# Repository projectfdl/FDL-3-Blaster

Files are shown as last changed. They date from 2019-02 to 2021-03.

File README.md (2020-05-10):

(https://www.projectfdl.com)

# FDL-3-Blaster

Welcome to the FDL-3 blaster repository

## This project is licensed under the terms of the Creative Commons Non-Commercial Attribution Share Alike 4.0 license
Print it, tweak it, share it and if you do and give us props. Please don't sell it without Project FDL permission.

<br>
<br>

# Operating your FDL-3

## Settings (Applicable to full auto tail, firmware version 1.05)

**Speed**<br>
Value: 0 - 100 : Default: 50<br>
Speed or power setting used to adjust the velocity the blaster fires darts.<br><br>

**ROF (Rate of Fire)**<br>
Value: 0 - 100 : Default: 100<br>
Rate of fire setting to adjust time between each dart fired when in burst or full auto.<br><br>

**Burst**<br>
Value: 1, 2, 3, F : Default: 1<br>
Number of darts fired per single trigger pull. F (full auto) will continue firing darts until you release the trigger.<br><br>

**MinSpin (Minimum Spinup)**<br>
Value: 120 - 500 : Default: 220<br>
Time in milliseconds for motors to spinup between trigger pull and firing dart when speed set to 0.<br><br>

**MaxSpin (Maximum Spinup)**<br>
Value: 150 - 500 : Default: 200<br>
Time in milliseconds for motors to spinup between trigger pull and firing dart when speed set to 100.
Note: MinSpin and MaxSpin together create a range of spinup time. When speed is set to 50, spinup time is half way between MinSpin and MaxSpin. Eg. MinSpin = 200, MaxSpin = 300, Speed = 50. Actual spinup time = 250. Speed = 75. Actual spinup time = 275.<br><br>

**Fire Mode**<br>
Value: SAFE, ABIDE, AUTO, CACHE : Default: ABIDE<br>
Setting for how the blaster reacts to a trigger pull prior to firing a dart.<br>
- Safe: safety mode. Blaster will beep and not fire dart.
- Abide: Trigger abide. Blaster will only fire a dart if trigger is held down for the full spinup duration. If trigger is released prior to the completion of spinupt time, the blaster will not fire.
- Auto: Blaster will fire dart automatically. If trigger is released prior to the completion of spinup time, the blaster will continue it's fire cycle and proceed to fire all darts set by the burst setting.
- Cache: Cached mode. The blaster will "cache" the number of trigger pulls during the spinup duration. If you are able to pull the trigger three times during spinup, the blaster will fire three darts. Twice, two darts. Once, one dart.<br><br>

**Spindown**<br>
Value: 7 - 18 : Default: 14<br>
Rate at which the blasters motors wind down or "spindown" to a stop. Lower is faster. Higher is slower. The value is technically equal to the time in milliseconds to lower the speed of the blaster by a single increment.<br><br>

**Idle (Idle Time)**<br>
Value: 0 - 10 : Default: 0<br>
After the end of a fire cycle the motors will spin at a slow idle speed for this number of seconds. This allows the motors to spinup faster than if they were to start from a dead stop. Setting this to 0 will disable the feature. Note: if the trigger is held down at the end of a fire cycle, the motors will run at this idle speed until trigger is released.<br><br>

**Load**<br>
Load user preset 1, 2, 3 or back out of menu.<br><br>

**Save**<br>
Save current blaster settings to one of three user preset slots which can be recalled later by the load menu or user buttons on the side of the blaster. Note: only settings prior before the Load menu item are stored in presets. Speed, ROF, Burst, MinSpin, MaxSpin, FireMode, Spindown and Idle.<br><br>

**MinSpd (Minimum Speed)**<br>
Value: 0 - 100 : Default: 0<br>
Determines the minimum speed value that may be set by the speed setting. Eg. if set to 25, the speed gauge will not go lower than 25.<br><br>

**MaxSpd (Maximum Speed)**<br>
Value: 0 - 100 : Default: 100<br>
Determines the maximum speed value that may be set by the speed setting. Eg. if set to 80, the speed gauge will not go higher than 80. Recalled presets with higher speed values will default to this setting. The last value this setting was set to prior to powering off the blaster can be locked by flipping the red speed lock switch located on next to the screen on the board in the rear of the blaster. The rear cap piece must be removed to access this switch. This value cannot be altered while the blaster speed lock is enabled.<br><br>

**BtnMode (Button Mode)**<br>
Value: PRESET, SPEED, ROF, BURST : Default: BURST<br>
Determines what the three user quick buttons on the side of the blaster do. These buttons must be briefly held down for action to take place.<br>
- Preset: Loads user preset. Front button loads preset 1. Rear button closed to user loads preset 3.
- Speed: Sets blaster speed. From front to rear button. 50, 75, 100
- ROF: Set blaster rate of fire. From front to rear button. 50, 75, 100
- Burst: Sets blaster burst count. From front to rear button. 1, 2, F<br><br>

**BrkAgr (Braking Aggression)**<br>
Value: 3 - 20 : Default: 16<br>
Determines how aggressively the pusher brakes prior to reaching a stop at the rear of its cycle. Setting lower may produce a more responsive cycle but may leave the pusher extended at the end of the cycle. Setting higher may resolve issues with a pusher that does not stop properly at the rear of its cycle. This setting should rarely need to change.<br><br>

**ULock (User Lock)**<br>
Enable complete blaster lockout by setting a user defined sequence of quick button presses. Blaster will not function once lock is set and may be unlocked by reentering the defined sequence. Note: do not forget your code. While it is possible to reset your blaster, the method of doing so is not described in this document.<br><br>

**Bright (Brightness)**<br>
Value: 0 - 100 : Default: 100<br>
Sets the brightness of the oled display. This is a very subtle change in a high light environment but more obvious in darker surroundings.<br><br>

**Sound**<br>
Value: OFF, ON : Default: ON<br>
Enables or disables audible beeping while navigating menus, loading presets etc.<br><br>

**BatOff (Battery Offset)**<br>
Value: -5 - 5 : Default: 0<br>
Offsets the read battery voltage in increments of 0.1 volts. This is only for use with legacy or self built blasters if a full 3s battery does not read 12.6 volts.<br><br>

**Info**<br>
Displays current firmware version.<br><br>

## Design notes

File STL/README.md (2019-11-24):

(https://www.projectfdl.com)

# Printing your FDL-3

Note: Use your best judgement when slicing nad printing parts. Consider how your printer operates best and what settings you normally use for strong but light parts. This readme should be used as a set of suggestions to get you started but every printer is different. 

- We use common 0.4mm nozzles at 0.2mm layer heights. If using a different size, adjust accordingly.
- We use mostly PLA filament. It prints easily and cleanly without much hassle but can warp in high temperature environments like a hot car. Any other material such as PETG or ABS can be used at your own discretion.
- We typically use 3-5 perimeters (1.2 - 1.6mm) on all parts. Most have 3 but extra are added for structural parts like barrel outers(5), handle cores(4), stock attachment(4) etc
- Infill should be roughly 20% using your favorite infill pattern. Honeycomb and gyroid are great options. Add extra for structural parts like barrel outers(40-50), stock attachment(30) etc
- Prints must be clean and accurate. Too high an extrusion rate can lead to tight fitting parts. Remove and clean any brims or support. Sanding should not be required but may help fitment in areas.
- No support should be necessary on any parts but can help parts with areas of long bridging. Ex. mag gripper and fat boi grip on the 40 nose
- Parts should all be oriented to print. Use your best judgement and don't be afraid to try other orientations.
- Brims are suggested on parts without a lot of bed contact. There are small strands of material across the edges of channels on some parts. These prevent brim from entering wire channels. This should be removed.
- The pusher housing cap has holes that need drilling. Use a 9/64" or xacto blade to clean.
- The pusher housing has holes in it that need drilling. Use a 3mm and 7mm bit or xacto to clean.
- The spinner has a hole in the side that should be tapped with a 10-32 tap. Be careful to keep tool clean and not overheat the part.

Good luck and make on!

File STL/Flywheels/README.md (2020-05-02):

(https://www.projectfdl.com)

# Flywheel Choice

Choose which flywheel to print based off your motor. We ship bundles and blasters with Lumenier LX2205 motors. These are identical in size to the RX2205 which the wheels were based on but purple instead of silver so for FDL-3's #0098+ choose the Lumenier file. FDL-3's prior to #0097 used black Vspec motors with four screws to mount the flywheels. Choose the vspec file for those. The EMAX file is for a motor that was going to be used but never was. It is there for historical purposes. Spacers are only required for the EMAX version and can be ignored. Flywheels for the HIR nose are different but labeled as such.

# Printing

(https://www.projectfdl.com)

Flywheels must be printed balanced and strong but also light weight. Here are a few suggestions for how to do so. 

- We use common 0.4mm nozzles at 0.2mm layer heights. If using a different size, adjust accordingly.
- 0.2mm layer or lower layer height
- We currently print all wheels in ABS. It is extremely heat resistant, impact tolerant and less dense than PLA or PETG thus lighter. It requires an enclosure around your printer and some care to get right but we found it to be our favorite flywheel material. It's also easy to machine for balancing purposes.
- PLA can be used for flywheels with some caveats. Given the short time and ease of use, those caveats may be more or less important in your situation. It can be susceptible to warping under heavy or summer time use but is stronger than PETG in this use. It also fails in a safe way by splitting at layer seams. Good luck getting that to happen though.
- PETG can be weak and shatter if not printed properly. It's higher heat resistance can help warping but use it at your own risk to avoid shattered flywheels, ouch.
- Use 3-4 perimeters. 3 can lead to lighter wheels but 4 will be reliably stronger. We use 4.
- Infill should be roughly 20%, rectilinear, rotated vertical/horizontal instead of the typical 45 degrees and centered on the wheel.
- Layer seams (called different things in different slicers) should be randomized to avoid a heavy side where all the seams line up. Slicers will typically hide these seams in corners. We want them scattered randomly. A "zitted" appearance is normal and can help grip on darts.
- Target roughly 10 gram weight per wheel. Heavier have more inertia and could potentially perform better but are more susceptible to imbalance and sluggish feel. Lighter are less susceptible to imbalance and quieter but provide less momentum.
- Not all flywheels printed in this manner will be perfect. A propeller balancer can be used to balance wheels or you can print multiples and choose the best two.

Good luck and make on!

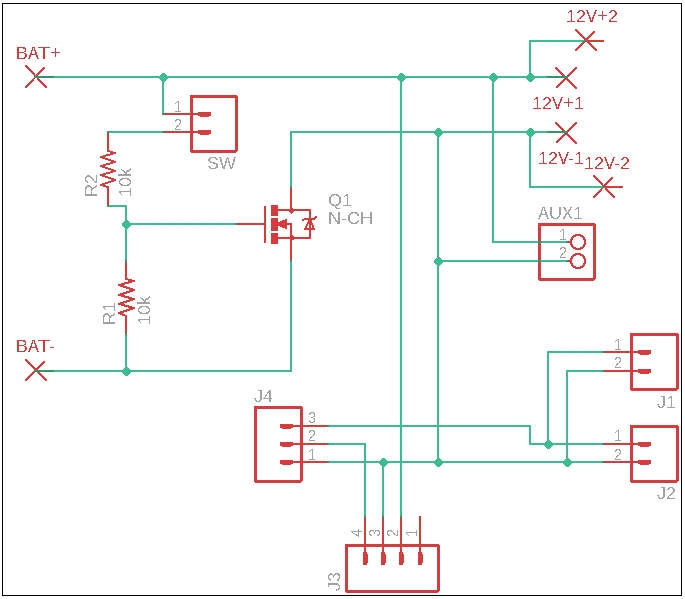
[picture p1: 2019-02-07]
PCB/PWR/FDL-3 PWR PCB Schematic.PNG

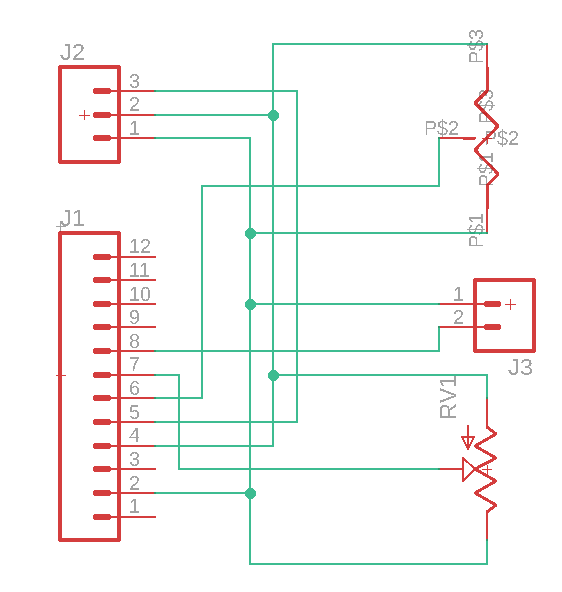
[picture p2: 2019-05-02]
PCB/TRG/FDL-3 TRG PCB Schematic.PNG

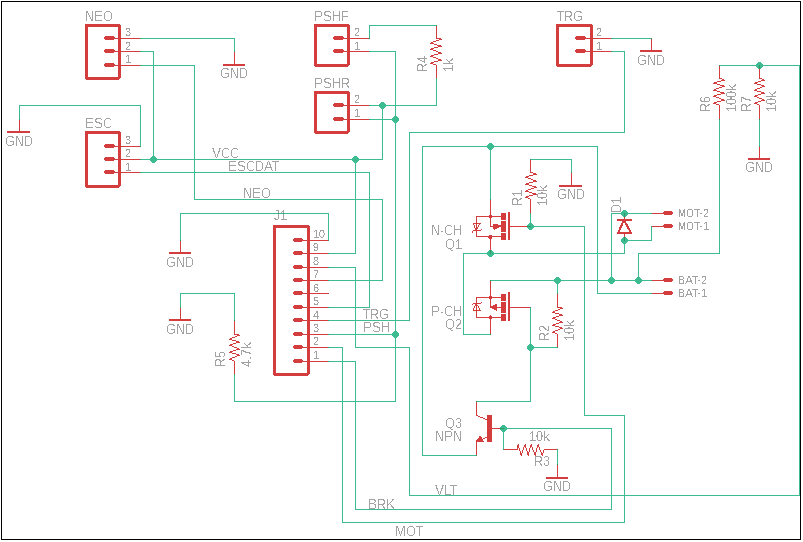
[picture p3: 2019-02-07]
PCB/DCP/FDL-3 DCP PCB Schematic.PNG

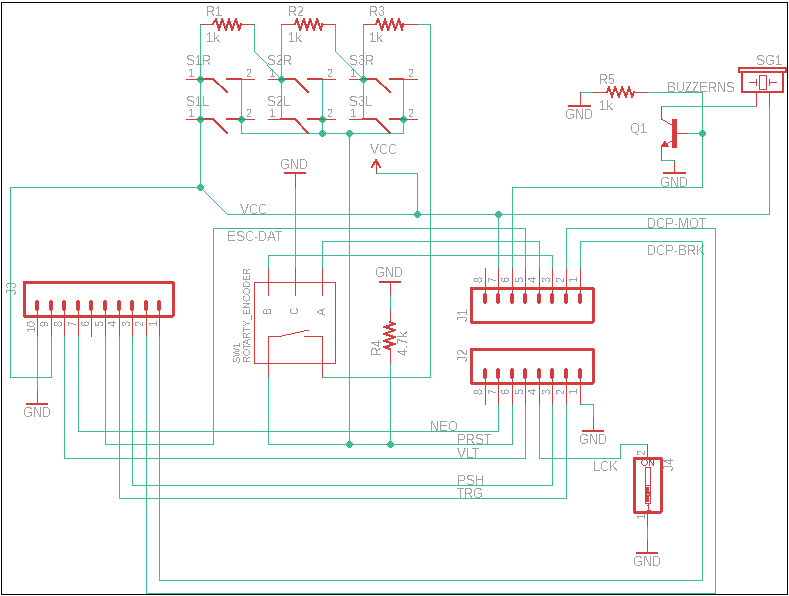
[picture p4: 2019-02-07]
PCB/CTL/FDL-3 CTL PCB Schematic.PNG

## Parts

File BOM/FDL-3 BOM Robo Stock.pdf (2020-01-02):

### FDL-3 ROBO STOCK BOM

Item | Quantity | Link

Hardware
6-32 x 3/8" Machine Screw | 4 | https://www.mcmaster.com/91249A146
6-32 x 1/2" Machine Screw | 4 | https://www.mcmaster.com/91249A148
8-32 x 1/2" Machine Screw | 4 | https://www.mcmaster.com/91249a194
8-32 Coupling Nut | 2 | https://www.mcmaster.com/90264a420
M5 Square Nut | 2 | https://www.mcmaster.com/90225a101
M5x70 Button Head Hex Screw | 2 | https://www.mcmaster.com/92095a484

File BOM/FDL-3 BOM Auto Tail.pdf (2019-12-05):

### FDL-3 AUTO TAIL BOM

Item | Quantity | Link

Hardware
6-32 x 3/8" Machine Screw | 18 | https://www.mcmaster.com/91249A146
6-32 x 1/2" Machine Screw | 9 | https://www.mcmaster.com/91249A148
6-32 x 1" Machine Screw | 1 | https://www.mcmaster.com/91249A159
6-32 Nut | 2 | https://www.mcmaster.com/91841A007
4-40 1-1/4" Hex Screw | 7 | https://www.mcmaster.com/92196A034
4-40 Nylon Lock Nut | 7 | https://www.mcmaster.com/91831A005
10-32 x 3/8" Set Screw Knurled End | 1 | https://www.mcmaster.com/93445A385
M3x6 Hex Screw | 8 | https://www.mcmaster.com/91290A111
Spring (Papermate InkJoy) | 1 | https://www.amazon.com/gp/product/B01EB6E3EC
M3x6 Csnk Hex Screw | 2 | https://www.mcmaster.com/92125A126
6-32 x 3/8" Thumb Screw | 2 | https://www.mcmaster.com/91185A261

DC Pusher Motor
25D Geared Motor ~1000RPM | 1 | https://www.pololu.com/product/3202
22ga Silicon Wire Red/Black Pair | 35cm | https://www.amazon.com/gp/product/B07DZZ83H6
JST Female Housing | 1 | https://www.pololu.com/product/1934
JST Female Crimp Connector | 2 | https://www.pololu.com/product/1934
3/32" Heat Shrink Red | 1.5" | (link unavailable - purchased locally)
3/32" Heat Shrink Black | 1.5" | (link unavailable - purchased locally)
1/8" Heat Shrink Black | 1" x 2 | (link unavailable - purchased locally)

DCP PCB
DCP PCB | 1 | https://projectfdl.myshopify.com/products/fdl-3-pcbs
N Channel Mosfet | 1 | https://www.digikey.com/products/en?keywords=IRLU3410PBF-ND
P Channel Mosfet | 1 | https://www.digikey.com/products/en?keywords=IRFU5505PBF-ND
Flyback Diode | 1 | https://www.digikey.com/product-detail/en/on-semiconductor/UF4007/UF4007CT-ND/965732
NPN Transistor | 1 | https://www.digikey.com/products/en?keywords=2N4401-ND
Header Male 2 Pin | 5 | https://www.pololu.com/product/965
Header Male 3 Pin | 1 | https://www.pololu.com/product/965
Header Female 10 Pin | 1 | https://www.digikey.com/product-detail/en/sullins-connector-solutions/PPTC101LFBN-RC/S7008-ND/810149
Resistor 1k 1/4W 6mm | 1 | https://www.digikey.com/product-detail/en/stackpole-electronics-inc/CF14JT1K00/CF14JT1K00CT-ND/1830350
Resistor 4.7k 1/4W 6mm | 1 | https://www.digikey.com/product-detail/en/stackpole-electronics-inc/CF14JT4K70/CF14JT4K70CT-ND/1830366
Resistor 10k 1/4W 6mm | 4 | https://www.digikey.com/product-detail/en/stackpole-electronics-inc/CF14JT10K0/CF14JT10K0CT-ND/1830374
Resistor 100k 1/4W 6mm | 1 | https://www.digikey.com/product-detail/en/stackpole-electronics-inc/CF14JT100K/CF14JT100KCT-ND/1830399

Control PCB
CTR PCB | 1 | https://projectfdl.myshopify.com/products/fdl-3-pcbs
Sparkfun Microview | 1 | https://www.sparkfun.com/products/12923
Rotary Encoder w/ Switch | 1 | https://www.digikey.com/products/en?keywords=PEC11R-4215K-S0024-ND
Tactile Switch Right Angle | 6 | https://www.digikey.com/products/en?keywords=450-1661-ND
Buzzer | 1 | https://www.digikey.com/product-detail/en/cui-inc/CEM-1201-50/102-1152-ND/412411
Single Position DIP switch | 1 | https://www.digikey.com/products/en?keywords=732-3831-5-ND
NPN Transistor | 1 | https://www.digikey.com/products/en?keywords=2N4401-ND
Header Male 10 Pin | 1 | https://www.pololu.com/product/965
Header Female 8 Pin | 2 | https://www.digikey.com/product-detail/en/sullins-connector-solutions/PPTC081LFBN-RC/S7006-ND/810147
Resistor 1k 1/4W 3.5mm | 4 | https://www.digikey.com/product-detail/en/te-connectivity-passive-product/CFR16J1K0/A104669CT-ND/3313506
Resistor 4.7k 1/4W 3.5mm | 1 | https://www.digikey.com/products/en?keywords=A105934CT-ND%E2%80%8E

PWR Switch
Power Switch 10A | 1 | https://www.digikey.com/products/en?keywords=RD1113112R-ND
Precrimped Wire Black 12" F-F | 2 | https://www.pololu.com/product/1850
Crimp Connector Housing 2 Pin | 2 | https://www.pololu.com/product/1901
1/8" Heat Shrink Black | 1" x 2 | (link unavailable - purchased locally)

ESC Extension
12" Servo Extension F-F | 1 | https://www.pololu.com/product/780

12V Extension
22ga Silicon WIre Red/Black Pair | 28cm | https://www.amazon.com/gp/product/B07DZZ83H6
JST Female Housing | 2 | https://www.pololu.com/product/1934
JST Female Crimp Connector | 4 | https://www.pololu.com/product/1934

Pusher Switch F
Microswitch | 1 | https://www.digikey.com/products/en?keywords=P10864S-ND
Precrimped Wire Gray 12" F-F | 2 | https://www.pololu.com/product/1848
Crimp Connector Housing 2 Pin | 1 | https://www.pololu.com/product/1901
1/16" Heat Shrink Black | 1" x 2 | (link unavailable - purchased locally)

### FDL-3 AUTO TAIL BOM

Item | Quantity | Link

Pusher Switch R
Microswitch | 1 | https://www.digikey.com/products/en?keywords=P10864S-ND
Precrimped Wire Green 6" F-F | 2 | https://www.pololu.com/product/1815
Crimp Connector Housing 2 Pin | 1 | https://www.pololu.com/product/1901
1/16" Heat Shrink Black | 1" x 2 | (link unavailable - purchased locally)

Trigger Button
Trigger Switch | 1 | https://www.digikey.com/products/en?keywords=SW151-ND
Precrimped Wire Orange 6" F-F | 2 | https://www.pololu.com/product/1813
Crimp Connector Housing 2 Pin | 1 | https://www.pololu.com/product/1901
1/8" Heat Shrink Black | 1" x 2 | (link unavailable - purchased locally)

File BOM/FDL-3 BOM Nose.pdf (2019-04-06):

### FDL-3 NOSE BOM

Item | Quantity | Link

Hardware
6-32 x 3/8" Machine Screw | 10 | https://www.mcmaster.com/91249A146
6-32 x 1/2" Machine Screw | 2 | https://www.mcmaster.com/91249A148
6-32 x 1" Machine Screw | 2 | https://www.mcmaster.com/91249A159
4-40 x 1-3/4" Hex Head Screw | 7 | https://www.mcmaster.com/92196A034
4-40 Nylon Lock Nut | 7 | https://www.mcmaster.com/91831A005
M3x6 Hex Screw | 8 | https://www.mcmaster.com/91290A111

PWR Group
PWR PCB | 1 | https://projectfdl.myshopify.com/products/fdl-3-pcbs
ESC - Spedix GS30 30amp | 2 | https://www.getfpv.com/spedix-gs30-30a-2-4s-blheli-32-dshot-esc.html
Brushless Motor - Lumenier LX2205 2400kv | 2 | https://www.getfpv.com/lumenier-lx2205-12-2400kv-motor.html
N Channel Mosfet 160AMP | 1 | https://www.digikey.com/products/en?keywords=IRLU8743PBF-ND
5V, 600mA Step-Down Voltage Regulator | 1 | https://www.pololu.com/product/3792
XT60 Male 16ga Pigtail | 1 | https://www.getfpv.com/yellow-xt60-lipo-pigtail-16awg-wire-5pcs.html
Resistor 10k 1/4w 3.5mm length | 2 | https://www.digikey.com/product-detail/en/te-connectivity-passive-product/CFR16J10K/A104668CT-ND/3313505
Crimp Connector Housing 2 Pin | 2 | https://www.pololu.com/product/1901
Header Male 2 Pin | 4 | https://www.pololu.com/product/965
Header Male 3 Pin | 1 | https://www.pololu.com/product/965

Disconnect Version Only
Silicon Wire 20ga Blk | 2" x 6 | https://www.amazon.com/BNTECHGO-Silicone-Flexible-Stranded-Impedance/dp/B01K4QVW1K
2mm Bullet Connector Male | 6 | https://hobbyking.com/en_us/2mm-gold-connectors-10-pairs-20pc.html
2mm Bullet Connector Female | 6 | https://hobbyking.com/en_us/2mm-gold-connectors-10-pairs-20pc.html
3/32" Heat Shrink Black | 1" x 12 | (link unavailable - purchased locally)

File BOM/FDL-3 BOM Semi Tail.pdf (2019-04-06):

### FDL-3 SEMI TAIL BOM

Item | Quantity | Link

Hardware
6-32 x 3/8" Machine Screw | 28 | https://www.mcmaster.com/91249A146
6-32 x 1/2" Machine Screw | 11 | https://www.mcmaster.com/91249A148
6-32 x 3/4" Machine Screw | 1 | https://www.mcmaster.com/91249A155
6-32 x 1" Machine Screw | 1 | https://www.mcmaster.com/91249A159
6-32 x 1-1/4" Machine Screw | 2 | https://www.mcmaster.com/91249A161
6-32 Nut | 2 | https://www.mcmaster.com/91841A007
4-40 x 1-3/4" Hex Screw | 1 | https://www.mcmaster.com/#92196A034
4-40 Nylon Lock Head Nut | 1 | https://www.mcmaster.com/#91831A005
Spring (Papermate InkJoy) | 1 | https://www.amazon.com/gp/product/B01EB6E3EC
Thumb Screw | 2 | https://www.mcmaster.com/91185A261
Trigger Spring | 1 | https://www.mcmaster.com/1986K618
Dowel Pin | 2 | https://www.mcmaster.com/98381A477

Trigger PCB
PCB TRG | 1 | https://projectfdl.myshopify.com/products/fdl-3-pcbs
6" Servo Extension F-F | 1 | https://www.pololu.com/product/779
10k Potentiometer Main | 1 | https://www.digikey.com/products/en?keywords=PTV09A-4015U-B103-ND
10k Potentiometer Limiter | 1 | https://www.digikey.com/products/en?keywords=3386F-103TLF-ND
Header Female Right Angle 12 pin | 1 | https://www.digikey.com/product-detail/en/sullins-connector-solutions/PPTC121LGBN-RC/S5448-ND/775906
Arduino Pro Mini 5v 16mhz | 1 | https://www.sparkfun.com/products/11113
Header Male 2 Pin | 1 | https://www.pololu.com/product/965
Header Male 12 Pin | 1 | https://www.pololu.com/product/965

PWR Switch
Power Switch 10A | 1 | https://www.digikey.com/products/en?keywords=RD1113112R-ND
Precrimped Wire Black 12" F-F | 2 | https://www.pololu.com/product/1850
Crimp Connector Housing 2 Pin | 2 | https://www.pololu.com/product/1901
1/8" Heat Shrink Black | 1" x 2 | (link unavailable - purchased locally)

Volt Meter
Volt Meter .28" | 1 | https://www.amazon.com/gp/product/B0761MG9NS
JST Extension 18" F-F | 1 | https://www.servocity.com/18-0-male-to-male-jst-extension

Trigger Switch
Trigger Switch | 1 | https://www.digikey.com/products/en?keywords=Z3631-ND
Crimp Connector Housing 2 Pin | 1 | https://www.pololu.com/product/1901
Precrimped Wire Orange 12" F-F | 2 | https://www.pololu.com/product/1843
1/8" Heat Shrink Black | 1" x 2 | (link unavailable - purchased locally)

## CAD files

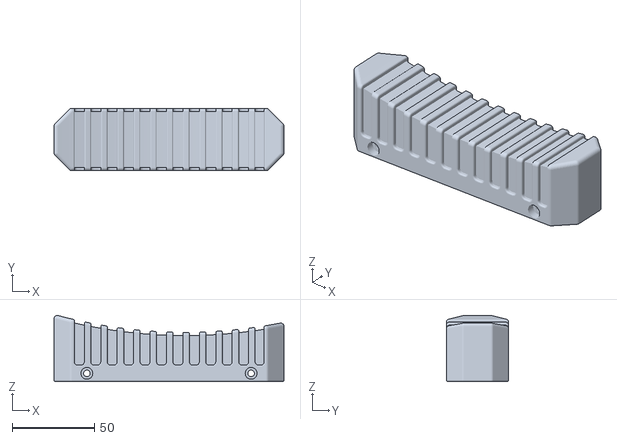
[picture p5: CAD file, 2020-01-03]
STL/Robo Stock/Butt Main.stl
140.0 x 38.0 x 40.2

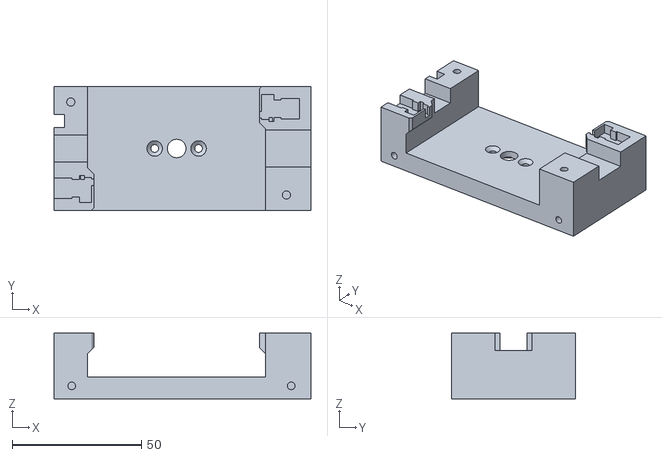
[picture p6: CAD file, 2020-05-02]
STL/Tail Auto/Pusher Housing Main.stl
99.5 x 48.0 x 25.4

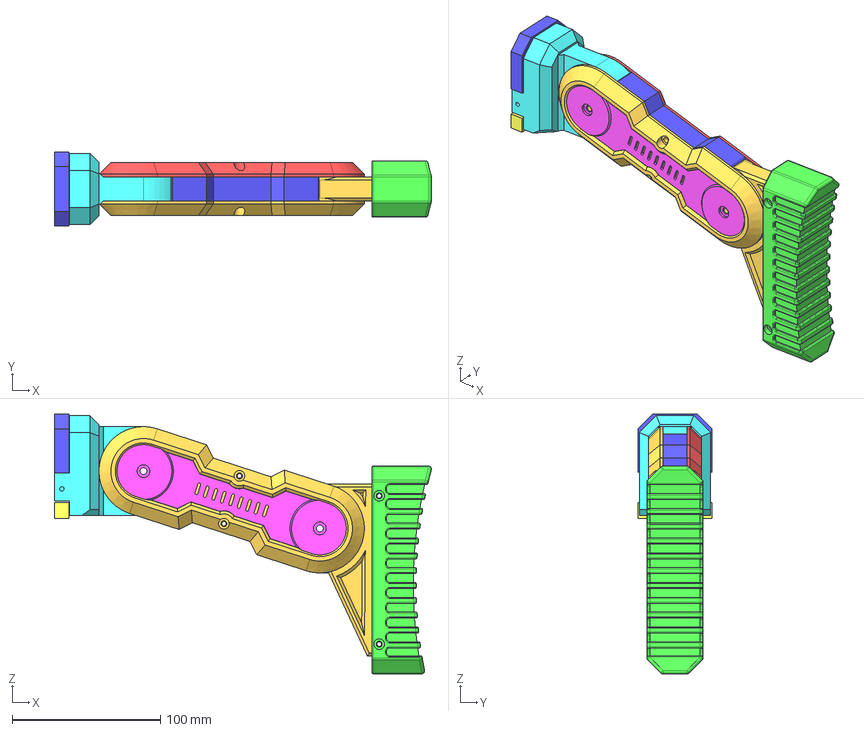
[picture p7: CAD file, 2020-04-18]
CAD/FDL-3 Robo Stock.step
254.1 x 50.0 x 175.0 mm

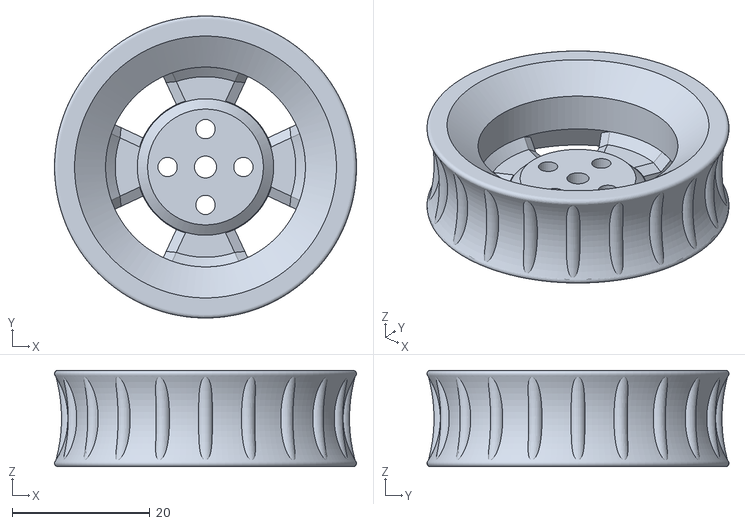
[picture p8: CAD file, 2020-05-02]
STL/Flywheels/Flywheel Crux HIR.stl
43.8 x 43.8 x 14.0

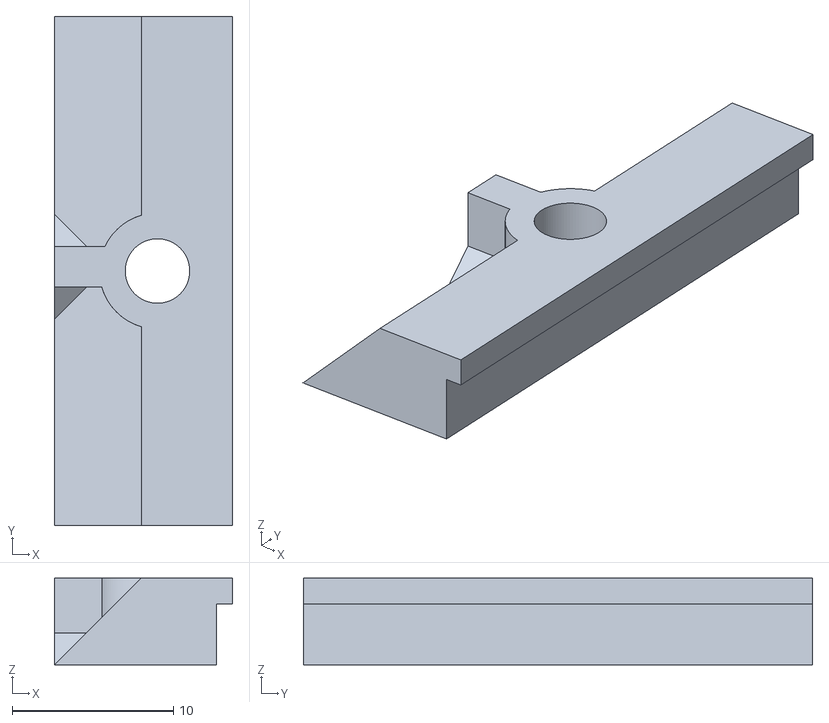
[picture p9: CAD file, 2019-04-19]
STL/Nose Forty/ESC Housing Clamp.stl
11.1 x 31.6 x 5.40

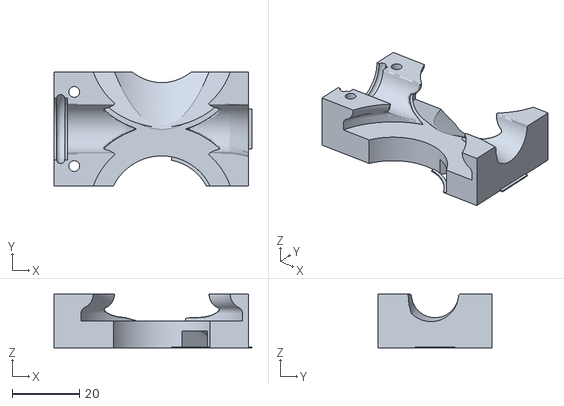
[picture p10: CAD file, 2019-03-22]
STL/Nose Full/Barrel Inner R.stl
58.8 x 34.0 x 16.0

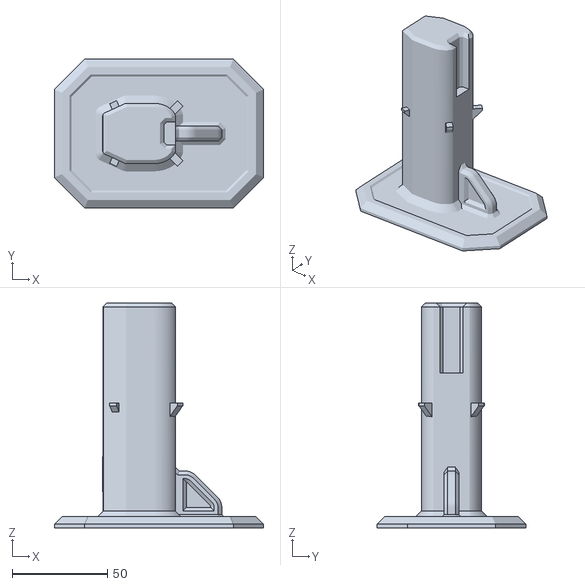
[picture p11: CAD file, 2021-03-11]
STL/Nose HIR/Blaster Stand HIR.stl
110.2 x 78.2 x 118.4

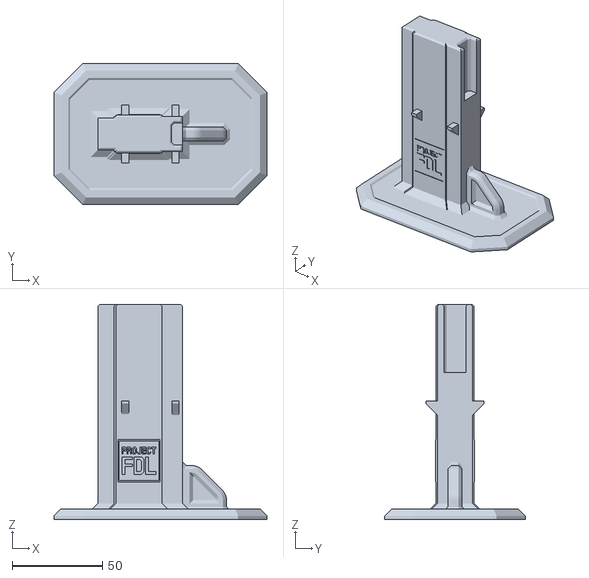
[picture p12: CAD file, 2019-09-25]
STL/Nose Shorty/Blaster Stand.stl
118.2 x 78.2 x 119.4

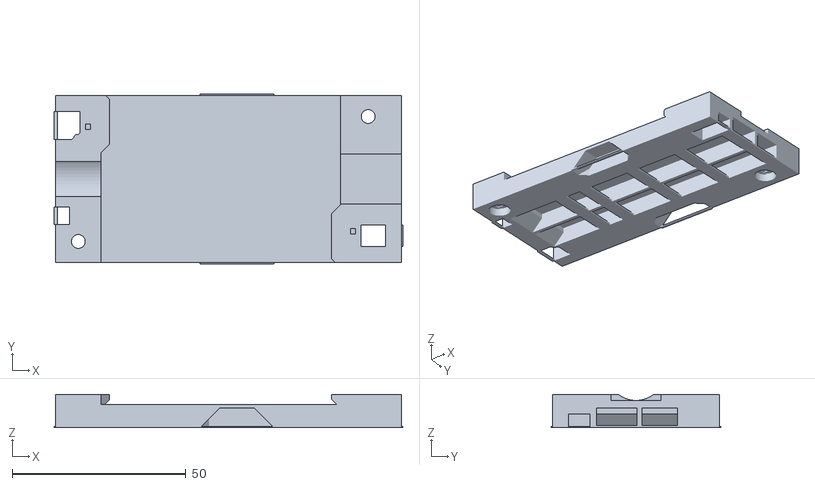
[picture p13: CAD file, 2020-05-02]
STL/Tail Auto/Pusher Housing Cap.stl
100.5 x 49.0 x 9.59

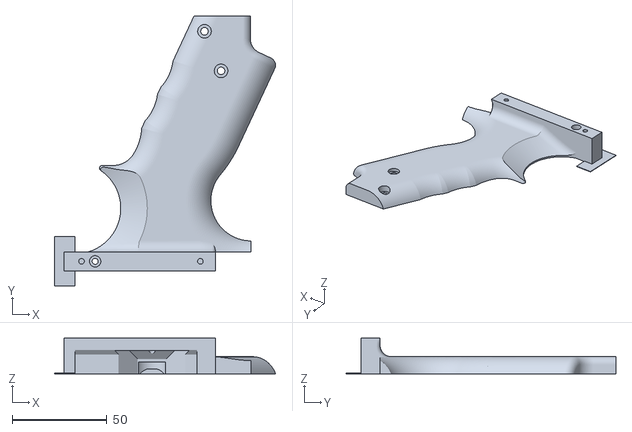
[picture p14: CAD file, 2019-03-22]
STL/Tail Semi/Handle Scale R.stl
116.7 x 142.4 x 18.8

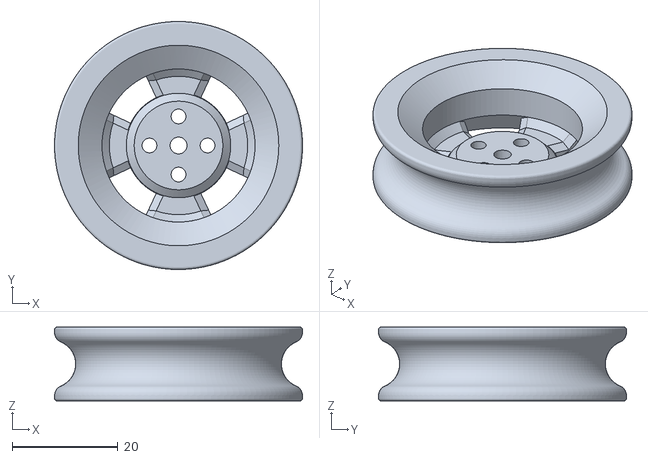
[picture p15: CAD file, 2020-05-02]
STL/Flywheels/Flywheel Crux 9mm.stl
47.0 x 47.0 x 14.0

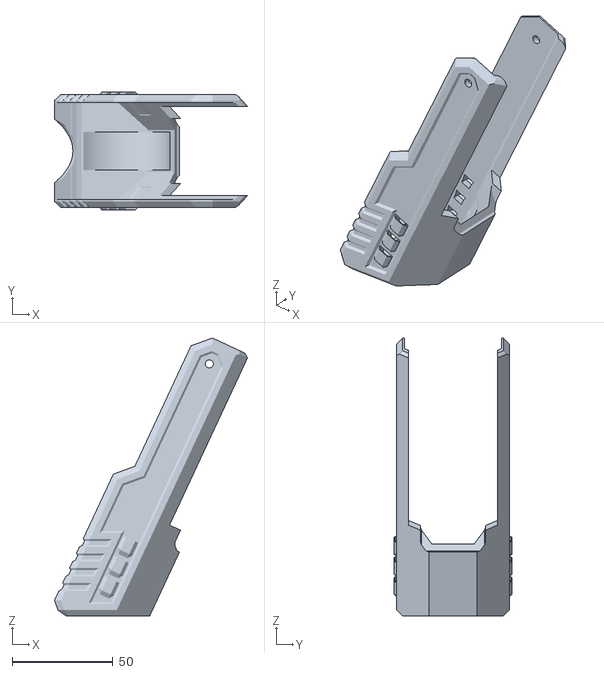
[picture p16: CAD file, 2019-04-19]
STL/Nose Forty/Cowl Lower.stl
95.6 x 58.4 x 137.7

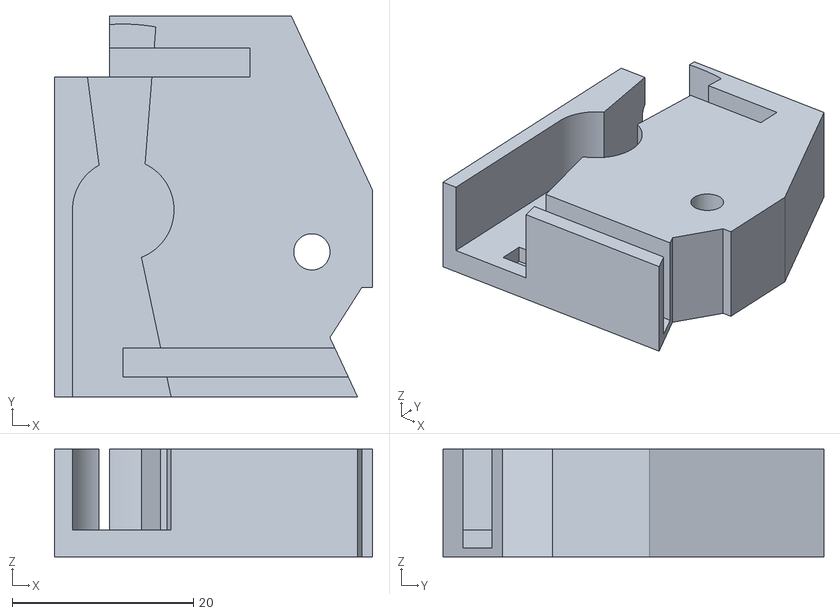
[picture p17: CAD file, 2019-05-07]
STL/Nose HIR/MagRel_Block.stl
35.1 x 42.0 x 11.9

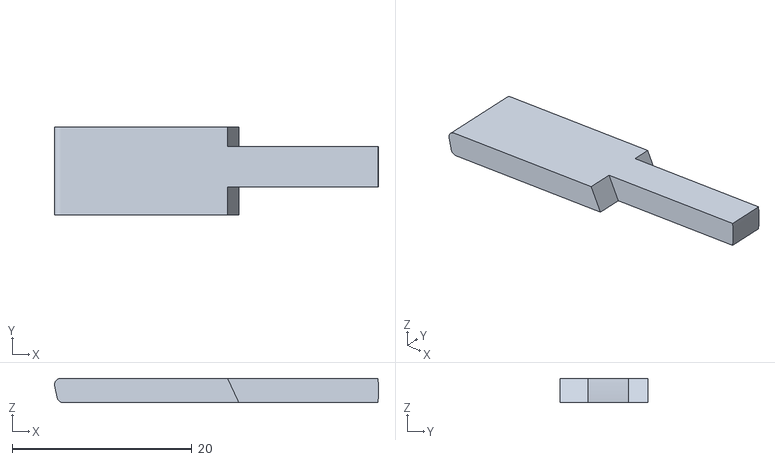
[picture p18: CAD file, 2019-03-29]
STL/Nose Shorty/MagRel Link Short.stl
36.0 x 9.80 x 2.70

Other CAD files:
STL/Nose Full/Barrel Inner L.stl
STL/Robo Stock/Butt Base.stl
STL/Tail Auto/Pusher.stl
STL/Tail Semi/Cap Mid.stl
STL/Flywheels/1.6mm spacer.stl
STL/Flywheels/2.0mm spacer.stl
STL/Flywheels/Flywheel Emax RS2205S 9mm.stl
STL/Flywheels/Flywheel Lumenier MB2206 9mm.stl
STL/Flywheels/Flywheel Lumenier RX2205 9mm.stl
STL/Flywheels/Flywheel Lumenier RX2205 HIR.stl
STL/Flywheels/Flywheel Vspec 2205 9mm.stl
STL/Nose Forty/Barrel Inner L.stl
STL/Nose Forty/Barrel Inner R.stl
STL/Nose Forty/Barrel Outer L.stl
STL/Nose Forty/Barrel Outer R.stl
STL/Nose Forty/Cowl Upper.stl
STL/Nose Forty/ESC Housing Cap.stl
STL/Nose Forty/ESC Housing.stl
STL/Nose Forty/Grip Fat Boi.stl
STL/Nose Forty/Mag Adapter.stl
STL/Nose Forty/MagRel Block.stl
STL/Nose Forty/MagRel Catch.stl
STL/Nose Forty/MagRel Lever.stl
STL/Nose Forty/MagRel Link Long.stl
STL/Nose Forty/MagRel Link Short.stl
STL/Nose Forty/MagRel Pivot.stl
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

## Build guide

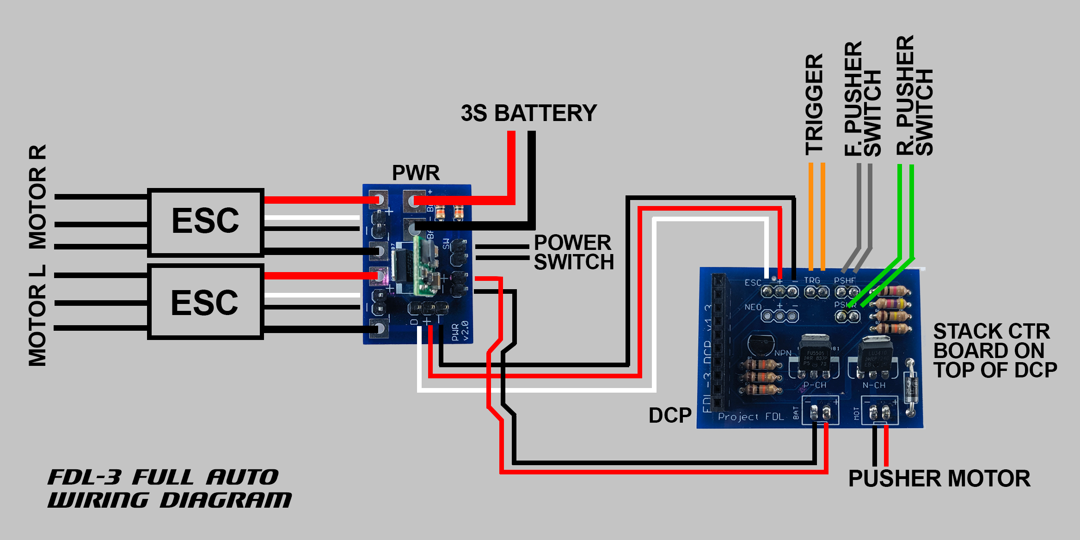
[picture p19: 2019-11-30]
PCB/FDL-3 Wiring Diagram.png

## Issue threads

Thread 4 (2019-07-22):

pusher motor interaction with switches and firmware

bmarks-mylo, 2019-07-22:
Looking at the pusher design and reading through the latest firmware I'm not sure I understand the interaction with the front/rear pusher switches and motor control.  I think I'm seeing that there is a  forward and reverse control circuit for the pusher motor but I can't seem to find where the firmware is using both directions.

Can you please give a brief explanation of the interaction of these components and the firmware?

bmarks-mylo, 2019-07-22:
Ok, I think I understand now.  The circuit acts as a brake to stop the motor from spinning faster.

My only remaining question is then why the need for a front and rear switch.  Why is knowing that the plunger is fully forward important?  Just a way to time it?

projectfdl, 2019-07-22:
The front switch is an indication that a full forward cycle has occured. From that point there is a short brake blip to slow it down and coast to the rear position if you are on your final shot. It is both timing and a self test. There is no reverse direction as that would require a full instead of half hbridge for minimal gain aside from maybe backing the pusher out in a jam like the original FDL-2 used to.

bmarks-mylo, 2019-07-22:
Excellent, thank you for the information.

Closed 2019-07-22.

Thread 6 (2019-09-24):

What is the difference between the full, shorty, HIR and forty noses?

xoxota99, 2019-09-24:
I guess I understand the difference between full auto and semi, and I guess "shorty" means shorter darts, but what are the HIR and "forty" options?

Jsanches8448, 2019-09-24:
HIR’s are the yellow balls. “Forty” is to fit the forty round mags.

xoxota99, 2019-09-25:
Thanks!

Closed 2019-09-25.

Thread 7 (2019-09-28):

Questions...

xoxota99, 2019-09-28:
Not sure where to ask these questions:
- What material should I use when printing these parts? PLA? PETG?
- What's the difference between the pusher, and the "Pusher 1mm dwell"?

43sunsets, 2019-09-28:
1. You can use whatever you like. PLA is the easiest to print with but vulnerable to heat -- try not to leave it in a hot car, or your parts may end up warped. PETG is still easy to print but has slightly better heat resistance. ABS is harder to print (typically requires an enclosure) and gives off noxious/toxic fumes, but is lighter and potentially stronger, and has much better heat resistance.

I personally print with PLA+, which is significantly stronger than regular PLA.

2. The pusher with 1mm dwell was an experimental part made in an attempt to resolve problems with the auto pusher intermittently coming to a rest partially extended, instead of being fully retracted. As far as I can tell the latest v1.04 firmware has now fixed the intermittent pusher retraction problem, so there's no need to use the test pusher with the extra dwell time. Just use the regular pusher.

Closed 2019-09-28.

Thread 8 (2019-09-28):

Possible issues with STL files?

xoxota99, 2019-09-28:
I'm intending to print my own FDL-3 (shorty nose, full-auto tail), and noticed a couple of things in the STL files that I'm not sure if they are issues or not. Could you help me understand whether this is intentional, or if I need to "fix" them somehow?

in STL/Tail Auto:
- **Pusher Housing Main.stl** : Seems to have no holes for the motor shaft or mounting screws.
- **Pusher Housing Cap.stl**: Seems to have little bits of flashing around the outside of the part, where the cutouts are.
- **Handle Scale L.stl**: Has some sort of 0.2mm-thick rectangle hanging off the end of it (toward the front of the blaster).
- **Handle Scale R.stl**: Same issue as above. Weird rectangle on the front end of it.
- **PCB Mount.stl**: Seems to have a thin strip of plastic across the bottom-front of the model, across the cutout below the mount for the power switch.

In the STEP files:
- There are a couple of extra parts (basically flat rectangles) underneath the PCB (inside the "PCB Mount" part) in the "FDL-3_Tail Auto" design that were not exported as STL files. Are these not needed?
- Bunch of miscellaneous floating screw heads in the "FDL-3_Tail Semi" design.

43sunsets, 2019-09-28:
@xoxota99 For the **Pusher Housing**, it lacks holes because you're meant to drill these out after printing. This allows the part to be printed without supports. If you lack a drill (like me), you can modify the STLs to have actual holes, and print the part with supports instead.

For everything else STL, the "bits of flashing" or thin strips of extra plastic are meant to act as selective brims, to aid bed adhesion -- or at least, that's my interpretation. You can cut these off using flush cutters after printing.

xoxota99, 2019-09-28:
Thanks! I wasn't sure if I should remove them, but I couldn't see how they were used in the STEP files. "selective brims" is a great idea, and makes sense.

What about those two mysterious rectangular plates under the pcb in the "Tail Auto" STEP file? Do I need those? They don't have a corresponding STL file.

43sunsets, 2019-09-29:
@xoxota99 Sorry, I'm not familiar with STEP files and loading it up in F360 I have no idea how to separate the components to view them so I'm not sure what the rectangular plates are. But if they're not amongst the STL files then you don't need to print them.

zafuquazar, 2019-12-31:
@xoxota99, can I ask you where you found the STEP files? In teh CAD folder, there are only .dwg files, which I cannot actually open in F360 - they open in a browser window only (even after uploading to F360). Thanks!

xoxota99, 2019-12-31:
@zafuquazar Good question! I know I downloaded them at some point (and have them in a Fusion 360 project), but now I can't find them anywhere on the web.

I've reached out to Jackie, to ask for permission to share the files I have. I'll let you know if/when I hear back.

zafuquazar, 2020-01-01:
Thank you very much! I would like to make a blaster using the motors that I already have, and I would love to work from the FDL3 STEP files so I don't have to model everything from scratch :)

43sunsets, 2020-01-01:
> @xoxota99, can I ask you where you found the STEP files? In teh CAD folder, there are only .dwg files, which I cannot actually open in F360

I can confirm that Fusion 360 can read DWG files, you need to **Upload** them as a new project. There's no STEP files because the DWG files are it.

zafuquazar, 2020-01-01:
Thanks!
Hmm, ok, maybe I am doing it wrong. I did create a new project in F360 and upload the .dwg files. But when i try to open them, they open in a a browser window instead of F360. I can view rotate, etc in the browser, but cannot edit them.
But perhaps I’m doing something wrong - I’ll try again.

43sunsets, 2020-01-01:
@zafuquazar Hmm yeah that's really odd, it shouldn't be opening in a browser at all, it should remain and open within F360. Good luck, hope you can get it working soon!

zafuquazar, 2020-01-01:
Ok, thanks! I use Solidworks at work every day, but I feel pretty noob-ish in F360. I’ll keep at it!

stukemanmini, 2020-01-01:
> Thank you very much! I would like to make a blaster using the motors that I already have, and I would love to work from the FDL3 STEP files so I don't have to model everything from scratch :)

I made a few small changes in F360 to my blaster before printing. Here's how I've done it:
Use the "Insert Mesh" to import the STL file as a wireframe.
Tell the project to "Do not capture design history". (This seems to be required to convert a wireframe to a solid body)
Use the "Convert to BRep" on the mesh to make the wireframe into a body.
Then re-enable the design history.

xoxota99, 2020-01-02:
@43sunsets Slight correction. Fusion360 *used to* be able to import .DWG files (back when I did it in September). They have recently introduced new licensing terms for hobbyists that removed this capability. Fortunately, I still have my original imported project, and Jackie has given me permission to share them as a one-off.

@zafuquazar I'll email a zip file with the exported STEP files to the email address in your github profile. Hope this helps.

xoxota99, 2020-01-02:
I'm going to resolve this issue, since the question has been answered. Thanks!

zafuquazar, 2020-01-02:
@xoxota99 And @43sunsets, thank you so much for your help! I did try again today and could not get the parts to open inside of F360 - I’m happy to know I’m not crazy :)

43sunsets, 2020-01-03:
> @43sunsets Slight correction. Fusion360 _used to_ be able to import .DWG files (back when I did it in September). They have recently introduced new licensing terms for hobbyists that removed this capability.

Oh I wasn't aware of that, that sucks that they did that 😰. I thought I was using the Hobbyist version but it turns out I'm on the Student version of F360, so that probably explains it.

Closed 2020-01-02.

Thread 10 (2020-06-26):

Convert PDF files to Markdown file format and add pictures

ViliusKraujutis, 2020-06-26:
For easier editing, it would be great to have MD files instead of PDF.
Also, adding pictures of each object in the BOM file would be better. E.g. I was looking to https://github.com/projectfdl/FDL-3-Blaster/blob/master/BOM/FDL-3%20BOM%20Nose.pdf and it was not clear to me, what is that "Nose" this BOM is about. How does it look like when assembled?

ViliusKraujutis, 2020-06-26:
Please add label "lowest" priority, since this is a nice to have.

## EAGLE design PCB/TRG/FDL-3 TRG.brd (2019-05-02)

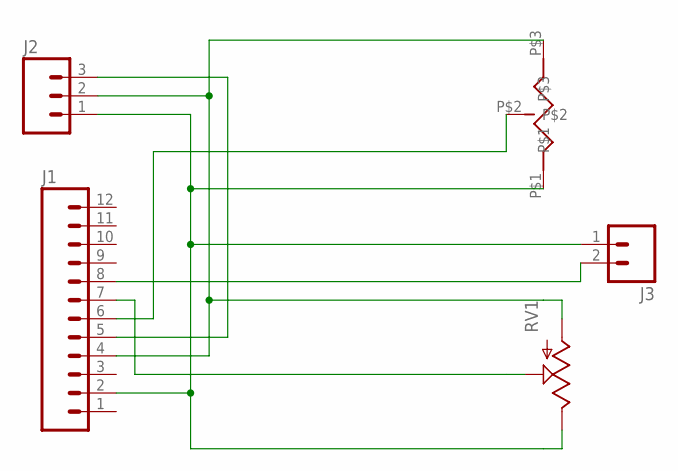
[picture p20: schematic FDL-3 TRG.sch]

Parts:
J1: M12LONGPADS; 1X12_LONGPADS
J2: M03LONGPADS; 1X03_LONGPADS
J3: M02PTH3; 1X02_LONGPADS
RV1: POTTRIM; TRIM_POT
U$1: THRUHOLEPOT

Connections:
unnamed: J1.2, J2.1, J3.1, RV1.2 (E), U$1.P$1
unnamed: J1.4, J2.2, RV1.3 (A), U$1.P$3
unnamed: J1.5, J2.3
unnamed: J1.6, U$1.P$2
unnamed: J1.7, RV1.1 (S)
unnamed: J1.8, J3.2

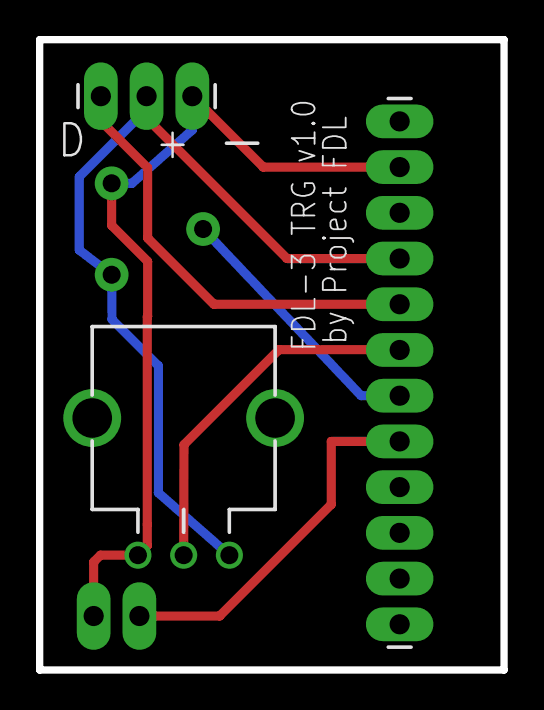
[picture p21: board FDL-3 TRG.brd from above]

Board: 2 copper layers, 25.8 x 35.0 mm, 5 parts (0 on the bottom side), 6 nets.

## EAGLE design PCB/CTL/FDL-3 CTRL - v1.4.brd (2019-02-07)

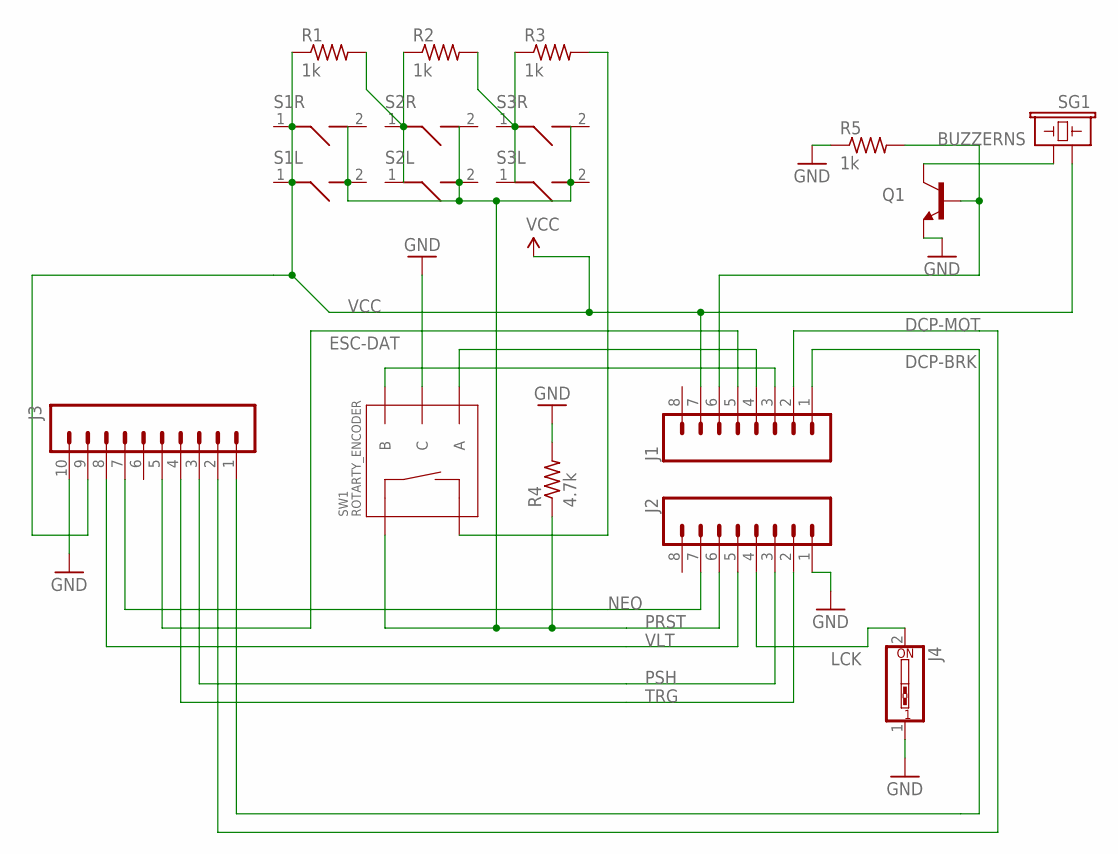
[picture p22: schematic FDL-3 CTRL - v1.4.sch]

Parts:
J1, J2: M08SILK_FEMALE_PTH; 1X08
J3: M10SILK_FEMALE_PTH; 1X10
J4: SW_DIP-1; EDG-01
Q1: TRANSISTOR_NPNBC547; TO-92-AMMO
R1, R2, R3, R5: 1k; 0204/5
R4: 4.7k; 0204/5
S1L, S1R, S2L, S2R, S3L, S3R: RGTANGTCTBTN
SG1: BUZZERNS; BUZZER-12MM-NS
SW1: ROTARTY_ENCODER; ROTARY_ENC_PLAIN

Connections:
DCP-BRK: J1.1, J3.1
DCP-MOT: J1.2, J3.2
ESC-DAT: J1.5, J3.5
GND: J2.1, J3.10, J4.1, Q1.3 (E), R4.2, R5.1, SW1.C
LCK: J2.4, J4.2
unnamed: R1.2, R2.1, S2L.1, S2R.1
unnamed: R2.2, R3.1, S3L.1, S3R.1
unnamed: R3.2, SW1.SW-
unnamed: Q1.1 (C), SG1.- (2)
unnamed: J1.4, SW1.A
unnamed: J1.3, SW1.B
unnamed: J1.6, Q1.2 (B), R5.2
NEO: J2.7, J3.7
PRST: J2.6, R4.1, S1L.2, S1R.2, S2L.2, S2R.2, S3L.2, S3R.2, SW1.SW+
PSH: J2.3, J3.3
TRG: J2.2, J3.4
VCC: J1.7, J3.9, R1.1, S1L.1, S1R.1, SG1.+ (1)
VLT: J2.5, J3.8

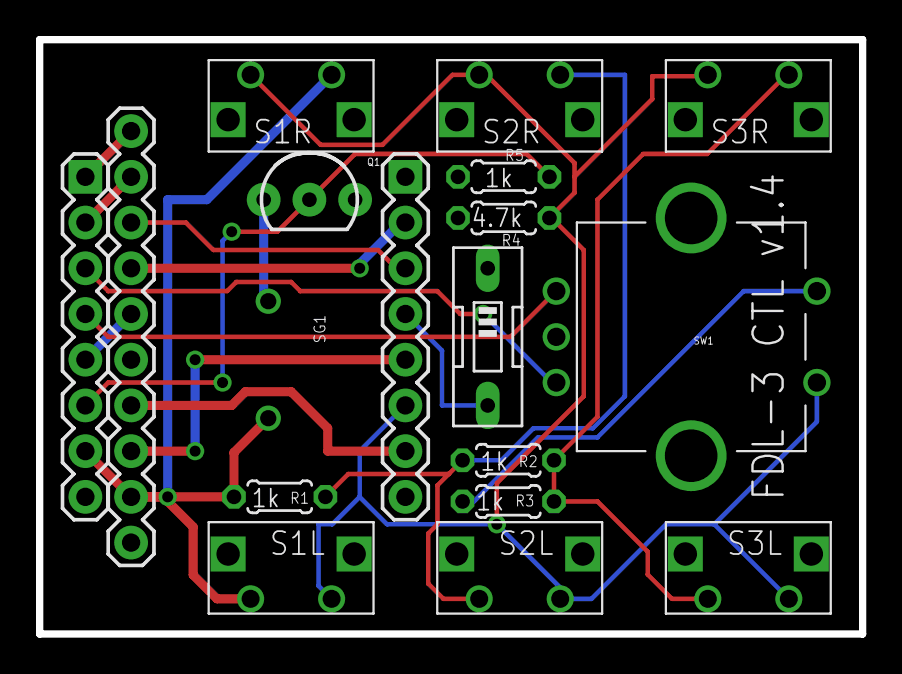
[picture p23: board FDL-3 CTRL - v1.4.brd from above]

Board: 2 copper layers, 45.7 x 33.0 mm, 18 parts (0 on the bottom side), 18 nets.

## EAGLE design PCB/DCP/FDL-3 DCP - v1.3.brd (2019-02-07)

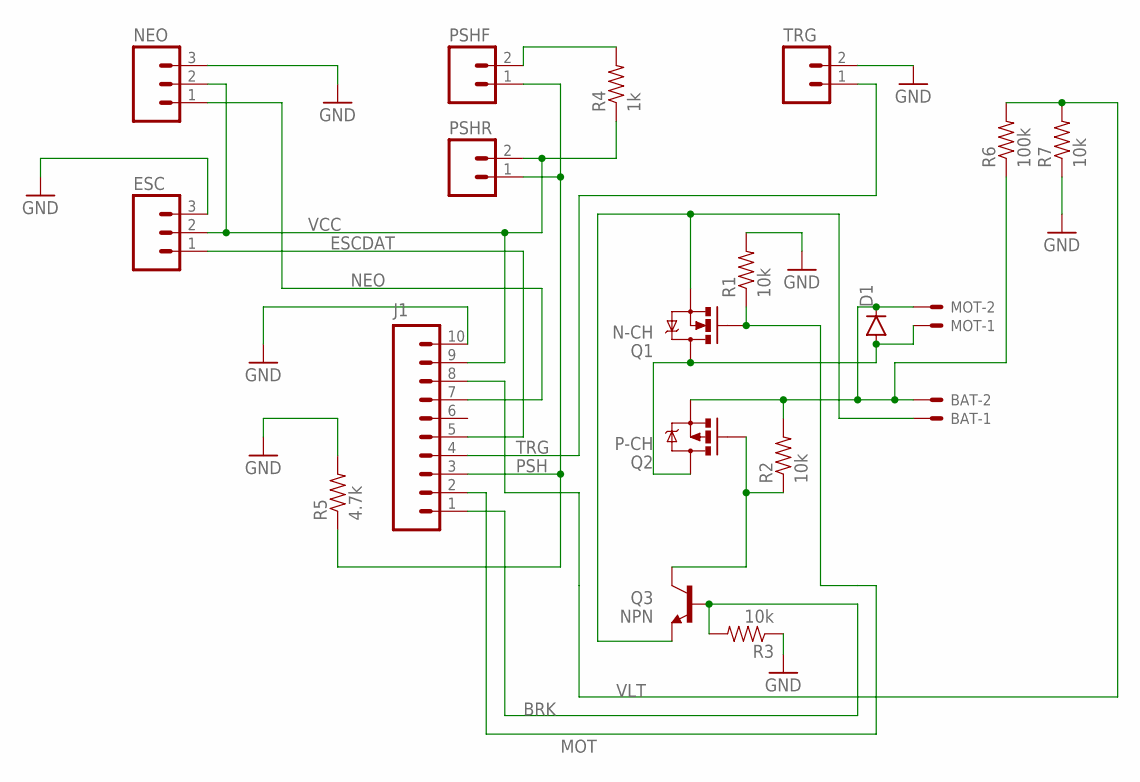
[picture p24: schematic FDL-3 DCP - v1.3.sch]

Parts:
BAT: JST-XH-02-PIN-LONG-PAD; JST-XH-02-PACKAGE-LONG-PAD
D1: DIODEPTH; DIODE-1N4001
ESC: M03PTH; 1X03
J1: M10SILK_FEMALE_PTH; 1X10
MOT: JST-XH-02-PIN-LONG-PAD; JST-XH-02-PACKAGE-LONG-PAD
NEO: M03PTH; 1X03
PSHF: M02PTH; 1X02
PSHR: M02PTH; 1X02
Q1: N-CH; TO220V
Q2: P-CH; TO220V
Q3: NPN; TO-92
R1, R2, R3, R7: 10k; AXIAL-0.3EZ
R4: 1k; AXIAL-0.3EZ
R5: 4.7k; AXIAL-0.3EZ
R6: 100k; AXIAL-0.3EZ
TRG: M02PTH; 1X02

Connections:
BRK: J1.1, Q3.2 (B), R3.P$2 (2)
ESCDAT: ESC.1, J1.5
GND: BAT.1, ESC.3, J1.10, NEO.3, Q1.3 (S), Q3.1 (E), R1.P$2 (2), R3.P$1 (1), R5.P$2 (2), R7.P$1 (1), TRG.2
MOT: J1.2, Q1.1 (G), R1.P$1 (1)
unnamed: Q2.1 (G), Q3.3 (C), R2.P$1 (1)
unnamed: BAT.2, D1.C, MOT.2, Q2.3 (S), R2.P$2 (2), R6.P$1 (1)
unnamed: D1.A, MOT.1, Q1.2 (D), Q2.2 (D)
unnamed: PSHF.2, R4.P$2 (2)
NEO: J1.7, NEO.1
PSH: J1.3, PSHF.1, PSHR.1, R5.P$1 (1)
TRG: J1.4, TRG.1
VCC: ESC.2, J1.9, NEO.2, PSHR.2, R4.P$1 (1)
VLT: J1.8, R6.P$2 (2), R7.P$2 (2)

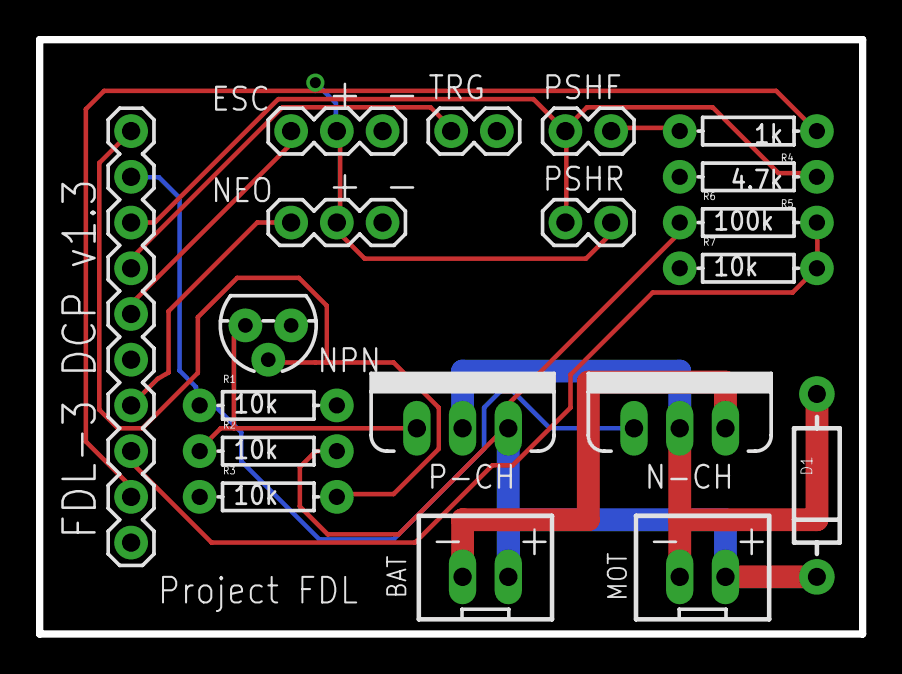
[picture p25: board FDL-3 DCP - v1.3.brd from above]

Board: 2 copper layers, 45.7 x 33.0 mm, 19 parts (0 on the bottom side), 13 nets.

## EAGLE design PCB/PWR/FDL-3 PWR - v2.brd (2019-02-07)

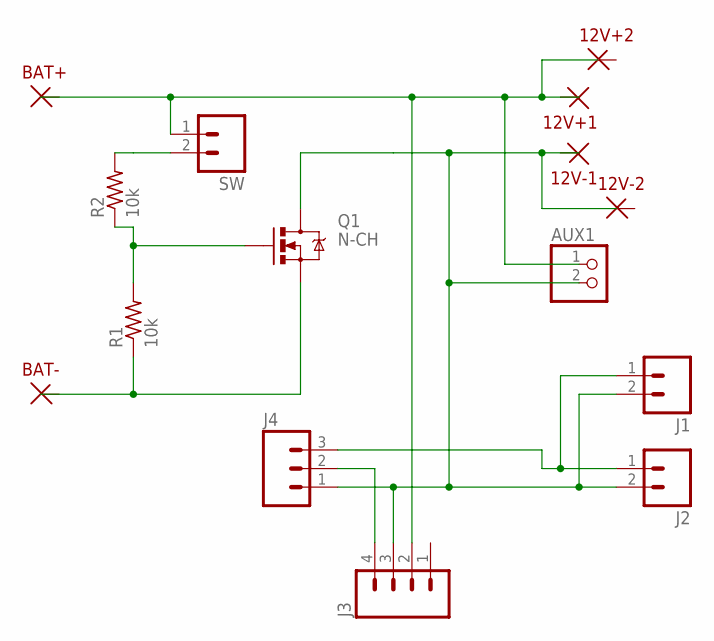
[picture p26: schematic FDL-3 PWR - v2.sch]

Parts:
12V+1, 12V+2, 12V-1, 12V-2: PWRPAD18
AUX1: PINHD-1X2; 1X02
BAT+: PWRPAD16
BAT-: PWRPAD16
J1, J2: M02PTH; 1X02
J3: M04PTH; 1X04
J4: M03PTH; 1X03
Q1: N-CH; TO220V
R1, R2: 10k; 0204/5
SW: M02PTH; 1X02

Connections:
unnamed: R2.2, SW.2
unnamed: J3.4, J4.2
unnamed: Q1.1 (G), R1.2, R2.1
unnamed: BAT-.P$1, Q1.3 (S), R1.1
unnamed: J1.1, J2.1, J4.3
unnamed: 12V+1.P$1, 12V+2.P$1, AUX1.1, BAT+.P$1, J3.2, SW.1
unnamed: 12V-1.P$1, 12V-2.P$1, AUX1.2, J1.2, J2.2, J3.3, J4.1, Q1.2 (D)

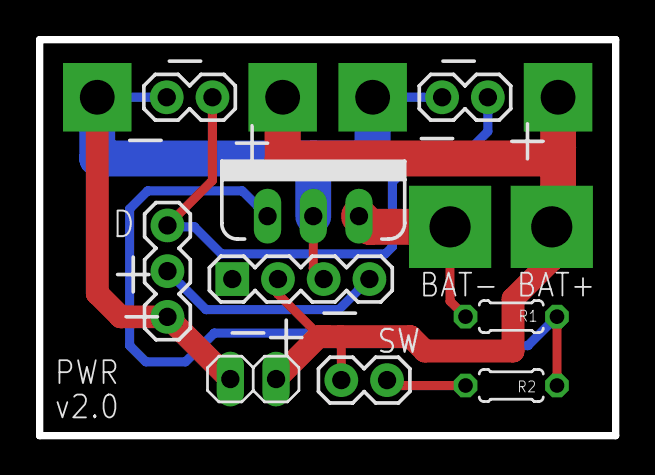
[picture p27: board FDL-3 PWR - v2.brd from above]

Board: 2 copper layers, 32.0 x 22.0 mm, 15 parts (0 on the bottom side), 7 nets.

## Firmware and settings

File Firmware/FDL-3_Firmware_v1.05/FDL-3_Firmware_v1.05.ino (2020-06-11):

/*
 FDL-3 Firmware v1.05 by Project FDL

 Libraries used:
 
 MicroView Arduino Library
 Copyright (C) 2014 GeekAmmo
 
 Encoder Library, for measuring quadrature encoded signals
 http://www.pjrc.com/teensy/td_libs_Encoder.html
 Copyright (c) 2011,2013 PJRC.COM, LLC - Paul Stoffregen <paul@pjrc.com>
*/

#include <MicroView.h>
#include <Encoder.h>
#include <EEPROM.h>
#include <Servo.h>

const byte versionNumber = 105;
const String splashText = "FDL-3"; //can be two lines split with space

Servo flywheelESC; 
Encoder myEnc(2, 3); 
MicroViewWidget *mainGauge;
MicroViewWidget *voltMeter;

#define NOTHROTTLE 1000
#define MINTHROTTLE 1285
#define MAXTHROTTLE 2000

//PINS
#define pusherBrakePin 0
#define pusherEnablePin 1
#define escPin 5
#define buzzerPin 6
#define triggerPin A0
#define pusherSwitchPin A1
#define lockPin A2
#define voltMeterPin A3
#define presetBtnPin A4

//MENUS
const char *knobMenu[] = 
{
  "Speed",
  "ROF",
  "Burst", 
  "MinSpin",
  "MaxSpin",   
  "FireMode",
  "Spindown",
  "Idle",
  "Load",
  "Save",
  "MinSpd",
  "MaxSpd",
  "BtnMode",
  "BrkAg",
  "ULock",
  "Bright",
  "Sound",
  "BatOff",
  "Info"    
};
byte knobMenuIndex = 0;

const char *burstMenu[] = {"1","2","3","F"};
const char *soundMenu[] = {"OFF","ON"};
const char *presetMenu[] = {"Back","1","2","3"};
const char *btnmodeMenu[] = {"PRESET","SPEED","ROF","BURST"};
const char *firemodeMenu[] = {"SAFE","TRIG","AUTO","CACHE"};
byte presetMenuIndex = 0;

//variables
bool liveKnobScrollMode = false;
bool menuBtnWasDown = false;
bool firstMenuRun = true;
bool speedLocked = false;
bool firstRun = true;
unsigned long lastSpinCheck = 0;
unsigned long lastSettingsSave = 0;
unsigned long lastBatAlarm = 0;
unsigned long brakeRelease = 0;
unsigned long idleRelease = 0;
long encoderChange = 0;
int currentSpeed = NOTHROTTLE;
int spindownTarget = NOTHROTTLE;

#define batteryCheckLength 6
float batteryCheck[batteryCheckLength];
unsigned long lastBatteryCheck = 0;
int batteryCheckIndex = 0;
float batteryCheckSum = 0.0;

struct StaticSettings {
  byte btnMode;
  int brightness;
  byte soundOn;
  int batOffset;
  int brkAgr;
  int usrLock;
  int minSpeed;
  int maxSpeed;
};
StaticSettings currStSettings = { 3, 100, true, 0, 16, 0, 0, 100 };
StaticSettings lastStSettings = { 3, 100, true, 0, 16, 0, 0, 100 };
StaticSettings defStSettings = { 3, 100, true, 0, 16, 0, 0, 100 };

struct BlastSettings {
  int speedValue;
  int rofValue;
  byte burstCount;
  int minSpinup;
  int maxSpinup;
  int spinDown; //units per ms for single value drop (higher = slower)
  int idleTime;
  byte fireMode;  
};
BlastSettings currBlSettings = { 50, 100, 0, 220, 220, 14, 0, 1 };
BlastSettings lastBlSettings = { 50, 100, 0, 220, 220, 14, 0, 1 };
BlastSettings readBlSettings = { 50, 100, 0, 220, 220, 14, 0, 1 };
BlastSettings defBlSettings = { 50, 100, 0, 220, 220, 14, 0, 1 };


void setup() {
  
  flywheelESC.attach(escPin); 
  flywheelESC.writeMicroseconds(0);  

  uView.begin();// start MicroView
  uView.clear(PAGE);
  uView.display();

  pinMode(voltMeterPin, INPUT);
  pinMode(presetBtnPin, INPUT);
  pinMode(pusherSwitchPin, INPUT);
  pinMode(triggerPin, INPUT_PULLUP);
  pinMode(lockPin, INPUT_PULLUP);
  pinMode(pusherEnablePin, OUTPUT);
  pinMode(pusherBrakePin, OUTPUT);
  pinMode(buzzerPin, OUTPUT);

  renderSplash(splashText);  
  loadSettings();

  if(presetButtonDown() == 4){
    int tmpLocVal = currStSettings.usrLock;
    clearSetRoutine();
    currStSettings.usrLock = tmpLocVal;
    writeStaticSettings();
  }

  if(lockOn() && presetButtonDown() == 3){
    clearLockRoutine();
  }

  mainGauge = new MicroViewGauge(16, 30, 0, 100, WIDGETSTYLE0 + WIDGETNOVALUE);
  voltMeter = new MicroViewSlider(56, 14, 106, 126, WIDGETSTYLE2 + WIDGETNOVALUE);

  mainGauge->reDraw();
  voltMeter->reDraw();

  initBatteryCheck(); 
  
  if(currStSettings.usrLock != 0){
    renderUserLock();
  }
  else{
    flywheelESC.writeMicroseconds(NOTHROTTLE);
    
    renderScreen();
    startUpBeeps();
    
    if(lockOn()){
      delay(500);
      toneAlt(3000, 150);
      delay(150);
      toneAlt(3000, 150);
      speedLocked = true;
    }
  }
}

void loop() {

  if(currStSettings.usrLock != 0){
    renderUserLock();
    return;
  }

  //cap speed at max
  if(currBlSettings.speedValue > currStSettings.maxSpeed){
    currBlSettings.speedValue = currStSettings.maxSpeed;
  }
  
  //check for trigger
  if(triggerDown() && millis() > 2800){
    fireSequence();
  }
  else{
    if(millis() > brakeRelease){
      digitalWrite(pusherBrakePin, LOW); 
      delayMicroseconds(200);
    }
    if(millis() > idleRelease){
      spindownTarget = NOTHROTTLE; 
    }
  }
   
  spinDownFW(false);  
  renderScreen();

  if(lastSettingsSave != 0 && millis() - lastSettingsSave < 2000){
     //don't save
  }
  else{
    if(currentSettingsChanged() || staticSettingsChanged()){
      writeCurrentSettings();
      writeStaticSettings();
      lastSettingsSave = millis();      
    }
  }
}

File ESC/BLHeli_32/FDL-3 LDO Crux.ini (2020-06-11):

[ESC0]
Eep_Name=
Eep_ESC_Layout=HTIRC_Hummingbird_32
Eep_ESC_Mode=2
Eep_FW_Main_Revision=32
Eep_FW_Sub_Revision=70
Eep_Layout_Revision=44
Eep_Pgm_Direction=1
Eep_Pgm_Rampup_Pwr=125
Eep_Pgm_Pwm_Freq=48
Eep_Pgm_Comm_Timing=28
Eep_Pgm_Demag_Comp=1
Eep_Pgm_Ppm_Min_Throttle=1040
Eep_Pgm_Ppm_Center_Throttle=1500
Eep_Pgm_Ppm_Max_Throttle=1960
Eep_Pgm_Enable_Throttle_Cal=0
Eep_Pgm_Temp_Prot_Enable=140
Eep_Pgm_Volt_Prot=0
Eep_Pgm_Curr_Prot=0
Eep_Pgm_Enable_Power_Prot=1
Eep_Pgm_Brake_On_Stop=0
Eep_Pgm_Beep_Strength=40
Eep_Pgm_Beacon_Strength=80
Eep_Pgm_Beacon_Delay=600
Eep_Pgm_LED_Control=0
Eep_Pgm_Max_Acceleration=0
Eep_Pgm_Nondamped_Mode=0
Eep_Pgm_Curr_Sense_Cal=100
Eep_Note_Config=48
Eep_Pgm_Sine_Mode=0
Eep_Pgm_Auto_Tlm_Mode=0
Eep_Pgm_Stall_Prot=1
Eep_Hw_Voltage_Sense_Capable=0
Eep_Hw_Current_Sense_Capable=0
Eep_Hw_LED_Capable_0=3
Eep_Hw_LED_Capable_1=2
Eep_Hw_LED_Capable_2=1
Eep_Hw_LED_Capable_3=0
Eep_Hw_Pwm_Freq_Min=255
Eep_Hw_Pwm_Freq_Max=255
Eep_Nondamped_Capable=1
Eep_Note_Array=C58C#58E58F58F#58G58G#58A58A#58B58C68A58A#58B58C68C78P8C78P4A68P4A78P4A68P4A78P4C78P4C78P4C78P4C78

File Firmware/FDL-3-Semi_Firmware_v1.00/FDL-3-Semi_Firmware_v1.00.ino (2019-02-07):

#include <Servo.h>
int escPin = A3;
int speedPin = A2;
int limiterPin = A1;
int triggerPin = A0;

Servo flywheelESC;

int currentSpeed = 1000;
int spindownRate = 10; //units per 10ms
unsigned long lastSpindownCheck = 0;
unsigned long elapsedTime = 0;

void setup() {
  pinMode(triggerPin, INPUT_PULLUP);
  pinMode(speedPin, INPUT);
  flywheelESC.attach(escPin); 
  flywheelESC.writeMicroseconds(1000);
}

// the loop function runs over and over again forever
void loop() {
 if(triggerDown()){

    int readSpeed = analogRead(speedPin);
    int limSpeed = analogRead(limiterPin);
    int maxSpeed = map(limSpeed, 0, 1023, 1285, 2000);
    int txSpeed = map(readSpeed, 0, 1023, 1285, maxSpeed);
  
    flywheelESC.writeMicroseconds(txSpeed);//1750);
    currentSpeed = txSpeed;
    elapsedTime = 0;
    lastSpindownCheck = millis();
  }
  else{
    //flywheelESC.writeMicroseconds(1000);
    spinDown();
  }

  //delay(2);
}

void spinDown(){

    int flipSpindown = (16 - spindownRate) * 2;
  
    if(currentSpeed > 1000){
      if(spindownRate == 0){
        currentSpeed = 1000;
      }
      else{
        elapsedTime = lastSpindownCheck == 0 ? 0 : elapsedTime + millis() - lastSpindownCheck;
        lastSpindownCheck = millis();
        int spindown = elapsedTime / 10 * flipSpindown;
        elapsedTime %= 10;
        
        currentSpeed -= spindown;
      }
    }
    
    flywheelESC.writeMicroseconds(currentSpeed);
}

boolean triggerDown(){
  return digitalRead(triggerPin) == LOW;
}

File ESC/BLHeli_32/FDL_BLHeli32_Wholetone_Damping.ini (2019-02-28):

[ESC0]
Eep_Name=
Eep_ESC_Layout=Spedix_GS30A_V1_1
Eep_ESC_Mode=2
Eep_FW_Main_Revision=32
Eep_FW_Sub_Revision=60
Eep_Layout_Revision=42
Eep_Pgm_Direction=1
Eep_Pgm_Rampup_Pwr=150
Eep_Pgm_Pwm_Freq=48
Eep_Pgm_Comm_Timing=16
Eep_Pgm_Demag_Comp=1
Eep_Pgm_Ppm_Min_Throttle=1040
Eep_Pgm_Ppm_Center_Throttle=1500
Eep_Pgm_Ppm_Max_Throttle=1960
Eep_Pgm_Enable_Throttle_Cal=0
Eep_Pgm_Temp_Prot_Enable=140
Eep_Pgm_Volt_Prot=0
Eep_Pgm_Enable_Power_Prot=1
Eep_Pgm_Brake_On_Stop=0
Eep_Pgm_Beep_Strength=40
Eep_Pgm_Beacon_Strength=80
Eep_Pgm_Beacon_Delay=600
Eep_Pgm_Max_Acceleration=0
Eep_Pgm_Nondamped_Mode=0
Eep_Note_Config=100
Eep_Pgm_Sine_Mode=0
Eep_Pgm_Auto_Tlm_Mode=0
Eep_Hw_Voltage_Sense_Capable=0
Eep_Hw_Current_Sense_Capable=0
Eep_Hw_LED_Capable_0=0
Eep_Hw_LED_Capable_1=0
Eep_Hw_LED_Capable_2=0
Eep_Hw_LED_Capable_3=0
Eep_Nondamped_Capable=1
Eep_Note_Array=C48D48E48F#48G#48A#48C58D58E58F#58G#58A#58D58E58F#58G#58A#58D68D48E48F#48G#48A#48D58

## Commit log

2019-02-05 first stl push
    [1.6mm spacer.stl, 2.0mm spacer.stl, Barrel Inner L.stl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]
2019-02-07 Firmware and PCB push
    [FDL-3 CTRL - v1.4.brd, FDL-3 CTRL - v1.4.sch, FDL-3 DCP - v1.3.brd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]
2019-02-07 Print orienting nose full stls
    [Barrel Inner L.stl, Barrel Inner R.stl, Barrel Outer L.stl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]
2019-02-07 Print oriented tail auto stls
    [Cap Mid NoNut.stl, Cap Mid.stl, Cap Rear.stl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]
2019-02-07 cad files initial push
2019-02-07 print oriented tail semi stls
2019-02-18 adding knob
    [Knob.stl]
2019-02-28 Updating for print orientation
    [Barrel Inner L.stl, Barrel Inner R.stl, Barrel Outer L.stl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]
2019-02-28 Updating print orientation
    [Barrel Inner L.stl, Barrel Inner R.stl, Barrel Outer L.stl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]
2019-02-28 Adding ESC firmware
2019-03-03 Fixing mag release pivot oddities
    [MagRel Pivot.stl]
2019-03-22 Part tweaks and print orientation
    [Barrel Inner L.stl, Barrel Inner R.stl, Cap Mid.stl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]
2019-03-29 Adding top rail to forty nose
    [Rail Top Front.stl]
2019-04-06 BOM upload
2019-04-06 Switch to xslx
    [FDL-3 BOM.xlsx]
2019-04-19 Mag fit tweaks
    [Cowl Lower.stl, ESC Housing Clamp.stl, Magwell.stl]
2019-05-02 Adding TRG PCB
    [FDL-3 TRG.brd, FDL-3 TRG.sch]
2019-05-07 Adding HIR nose files
    [Barrel Inner L.stl, Barrel Inner R.stl, Barrel Outer L.stl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]
2019-07-28 Updating flywheels and mock motors to lumenier versions
2019-08-31 Adding pivot file to forty fose stls
    [MagRel Pivot.stl]
2019-09-21 Adding 2206 flywheel
    [Flywheel Lumenier MB2206 9mm.stl]
2019-09-25 Adding logo to shorty blaster stand
    [Blaster Stand.stl]
2019-11-09 Fixed BOM links
    [FDL-3 BOM.xlsx]
2019-11-24 Add printing readme
2019-12-05 Updating resistor quantities, adding pdfs
    [FDL-3 BOM.xlsx]
2019-12-08 Updating trigger with small chamfer
    [Trigger.stl]
2019-12-08 removing dwell pusher
    [Pusher 1mm Dwell.stl]
2020-01-02 Adding Robo Stock
    [Arm Core.stl, Arm Insert.stl, Arm Panel.stl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]
2020-01-03 Orienting for print
    [Butt Base.stl, Butt Main.stl]
2020-04-18 Replace dwg cad files with f3d and step
    [FDL-3 Robo Stock.step]
2020-05-02 Adding crux wheels updating pusher componenets for no drill and tap
    [Flywheel Crux 9mm.stl, Flywheel Crux HIR.stl, Flywheel Lumenier RX2205 HIR.stl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]
2020-05-02 Orienting pusher housing cap for print
    [Pusher Housing Cap.stl]
2020-06-11 Add Crux ESC firmware ini
2021-03-11 Add HIR blaster stand stl
    [Blaster Stand HIR.stl]

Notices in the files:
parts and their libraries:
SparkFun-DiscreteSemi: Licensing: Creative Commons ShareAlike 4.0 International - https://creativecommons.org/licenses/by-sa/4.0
